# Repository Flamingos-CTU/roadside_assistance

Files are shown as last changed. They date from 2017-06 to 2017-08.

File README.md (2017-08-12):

# Roadside Assistance
Robot project repository for the Roadside Assistance competition on [Robot Day event](http://roboticday.org/2017/en/).

*Note: There is a hardware [notes](http://rtime.felk.cvut.cz/robot/index.php/M-BITBEAM_robot_kit) related to the robot and [m-bitbeam](http://www.tfsoft.cz/m-bitbeam/index_en.html) construction bit.*

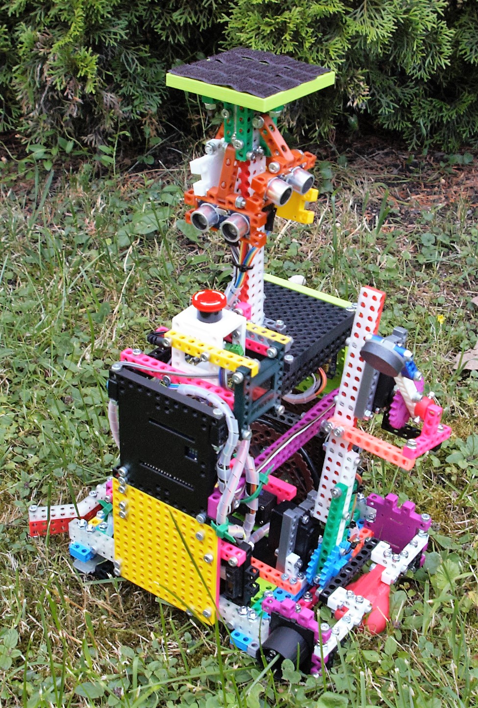
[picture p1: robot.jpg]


# Bit assistant

## Mission (impossible?)

The Roadside assistance contest is understood to be quite complicated and difficult.
Many robot creators think that a highly advanced control systems and algorithms, complicated electronics and mechanical design are needed to create a robot that can successfully attend this contest. Because of this there were not too many competitors to this contest to date.
We would like to change that and with our robot we want to present to the public that it can be done in a simple way.

Our goal is to build a robot from cheap and easily available components.
We want to build the robot as simple as possible yet potentially extensible to finish more tasks in the future.

## Robot

### Mechanical part

The robot construction is build exclusively from plastic 3D-printed parts connected with metal bolts and nuts.
These parts come from an open-hardware building kit called m-BITBEAM.
Source files for all the parts are freely available for download on GitHub (https://github.com/e-Mole/m-Bitbeam_Parts_for_3Dprint).
Any part can be easily reproduced/printed if needed.

The building kit is partially compatible with LEGO Technics/Mindstorms - the split of the mounting holes is the same.

The chassis uses a standard differential construction with two wheels and one support ball.

On the back of the robot is a robotic arm with three joints. Two of them are powered using servo motors. The end of the arm is fitted with a permanent magnet.
The arm is used to pick-up a spare battery and load it into the electric car.

### Hardware / electronics

#### Control logic

The control system of the robot is designed as a very simple distributed system comprising two Arduino boards.
The main control algorithm is programmed into Arduino UNO board with Servo shield attached.
This board drives all the servo motors and collect data from some sensors.

A second Arduino NANO board is used purely as a sensor gateway. It reads data from sensors and transmit the data to the main board.
The two Arduino boards are connected using simple serial line.

#### Sensoric sub-system

The robot is equipped with these sensors:
- 4x ultrasound module - used to detect the opponent.
- 2x infrared distance sensor on sides - used to detect playing elements (cars and batteries).
- 7x infrared reflective sensor at the bottom - used to detect color changes of the background of the playing field.
- 2x color sensor on sides - used to detect color of the electric cars.

#### Display, signalization, debuging

A small OLED graphic display is used to display various data.

Measured values from all the sensors and actual state of the control automaton are periodically transmitted on the USB-serial line.

#### Power supply

All the electronic components are supplied from a 5xAA NiMH battery pack.

### Software

The robot is based on the reactive paradigm. There is no environment map in the robot's memory. Just go ahead and follow the sensors' values.

Robot's behavior is implemented using finite state machines. We used feature-rich and powerful library Automaton. It also provides an extension for servo control. We implemented several separated automatons to control the robot:
* match automaton - starts the robot, check end of the match, handles sensor data received from sensor board,
* motion control automaton - drive servos and check the opponent to avoid a collision,
* automaton for a particular task, e.g. push_the_truck automaton handles such states as go_to_the_road, turn_on_the road, follow_the_road and push_the_truck.

Our software is available under the open source license. Go to Github and check it:) (https://github.com/Flamingos-CTU/roadside_assistance)

#### Tools

Software used in the robot was created using Arduino IDE. We also used a lot of freely available libraries and managed them by library manager built-in in Arduino IDE. We use Git for source code, hardware design and documentation versioning.

## About us

Our team is formed by three members - Matouš Pokorný, Michal Vokáč and Tomáš Novák.
We are a union of remnants of two independent teams - Flamingos and Gymspit.
We are also members of the organizational team of the Robotic Day.

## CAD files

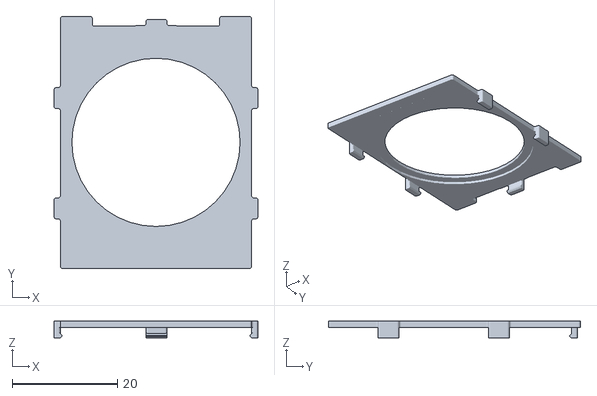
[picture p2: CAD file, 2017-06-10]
hw/colorSensor/lid.stl
38.8 x 48.0 x 3.20

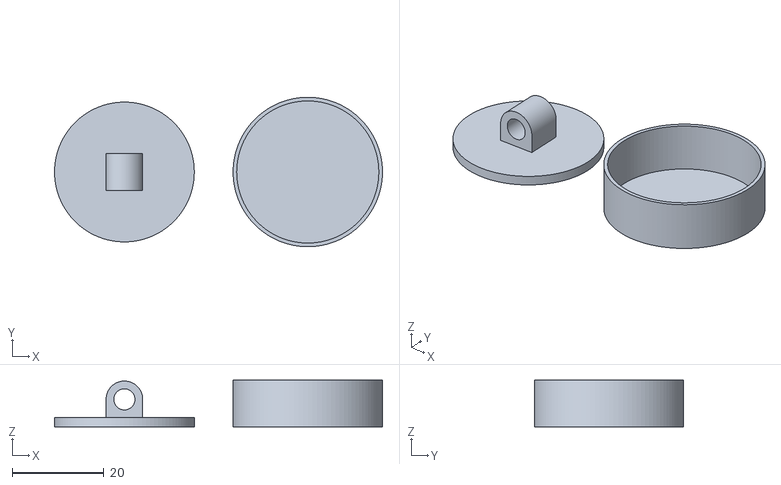
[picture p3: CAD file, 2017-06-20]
hw/magnet-holder/magnet-holder.stl
71.5 x 32.6 x 10.2

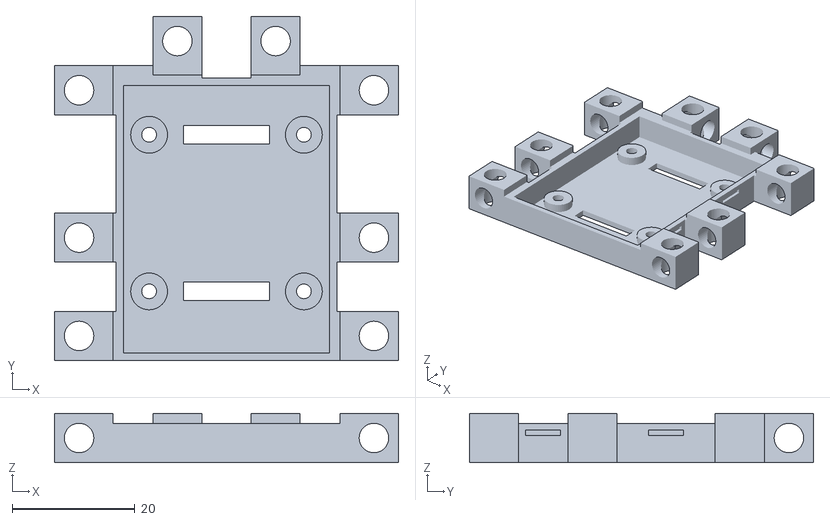
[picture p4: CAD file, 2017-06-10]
hw/colorSensor/box.stl
56.0 x 56.0 x 8.00

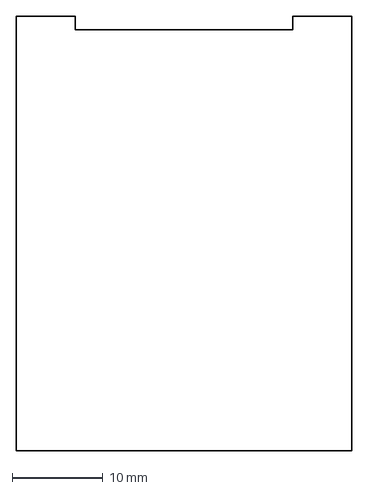
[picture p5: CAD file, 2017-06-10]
hw/colorSensor/molebox.dxf
37.0 x 48.0 mm

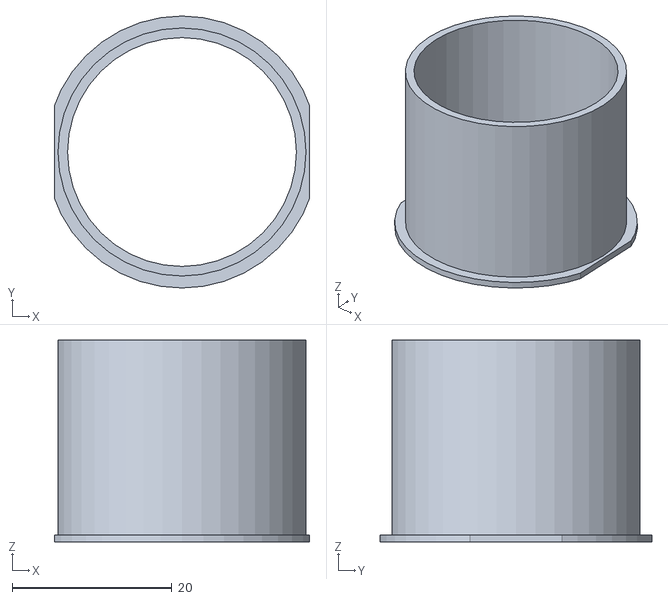
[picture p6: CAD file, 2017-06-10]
hw/colorSensor/cone.stl
31.9 x 34.0 x 25.2

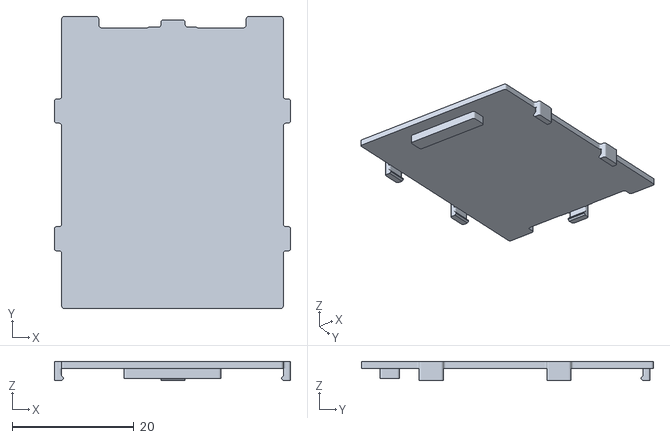
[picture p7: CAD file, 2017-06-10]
hw/colorSensor/bb-sen-uni-bt-c.stl
38.8 x 48.0 x 3.20

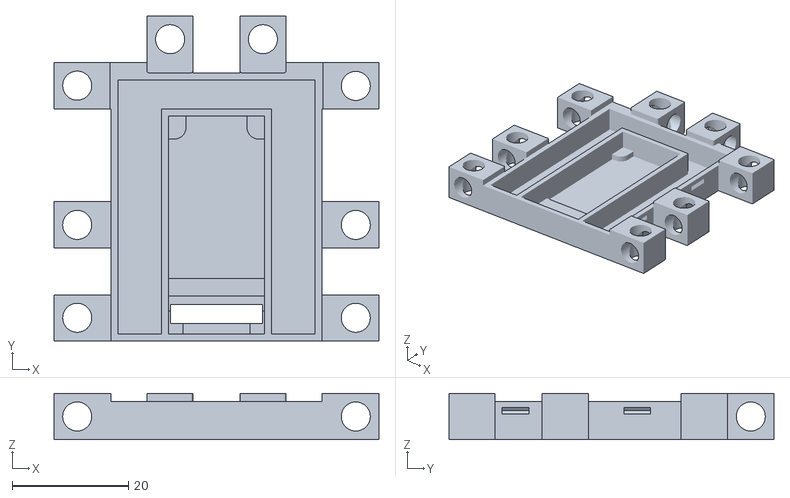
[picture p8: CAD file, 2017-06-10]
hw/colorSensor/bb-sen-uni-bt.stl
56.0 x 56.0 x 8.00

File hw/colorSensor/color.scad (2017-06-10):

$fn=40;
color([1,0,0]) colorbox();
color([0,0,1]) topcone();
lid();

module colorbox(){
    difference(){union(){
    basebox();
    translate([(28.4-3.2)/2,(28.7-3.2)/2,3/2])cylinder(d=6,h=3,center=true);
    translate([(28.4-3.2)/2,-(28.7-3.2)/2,3/2])cylinder(d=6,h=3,center=true);
    translate([-(28.4-3.2)/2,(28.7-3.2)/2,3/2])cylinder(d=6,h=3,center=true);
    translate([-(28.4-3.2)/2,-(28.7-3.2)/2,3/2])cylinder(d=6,h=3,center=true);
    }
    translate([(28.4-3.2)/2,(28.7-3.2)/2,2])cylinder(d=2.4,h=5,center=true);
    translate([(28.4-3.2)/2,-(28.7-3.2)/2,2])cylinder(d=2.4,h=5,center=true);
    translate([-(28.4-3.2)/2,(28.7-3.2)/2,2])cylinder(d=2.4,h=5,center=true);
    translate([-(28.4-3.2)/2,-(28.7-3.2)/2,2])cylinder(d=2.4,h=5,center=true);
    translate([0,-(28.7-3.2)/2,0])cube([14,3,4],center=true);
    translate([0,(28.7-3.2)/2,0])cube([14,3,4],center=true);
    }
}


module lid(){
difference(){translate([-100+8,-48/2,0])import("bb-sen-uni-bt-c.stl");
    cylinder(h=20,d=32);
    translate([0,-20,(8-1.2)/2-0.205])cube([25,10,8-1.2],center=true);
    cylinder(d=36,h=7.1);
    }
}
    
module topcone(){
    intersection(){
    translate([0,0,5])difference()
    {union(){
        translate([0,0,0.45])cylinder(d=34,h=0.9,center=true);
        translate([0,0,25.25/2])cylinder(d=31,h=24+1.25,center=true);
        }
        translate([0,0,25.25/2])cylinder(d=31-2.4,h=24+1.25+0.2,center=true);
        }
        linear_extrude(height=400)scale([0.95,0.95,1])translate([-56/2,-48/2,0])import("molebox.dxf",layer="innerbox");
    }
    }
module basebox(){
    translate([-56/2,-48/2,0])difference(){linear_extrude(height=8) import("molebox.dxf",layer="0",convexity=10);
translate([0,0,1.25])linear_extrude(height=8) import("molebox.dxf",layer="innerbox");
translate([0,0,6.35])linear_extrude(height=8) import("molebox.dxf",layer="lid",convexity=10);
    translate([4,4,4]) doublehole();
    translate([4,4+16,4]) doublehole();
    translate([4,4+40,4]) doublehole();
    translate([4+48,4,4]) doublehole();
    translate([4+48,4+16,4]) doublehole();
    translate([4+48,4+40,4]) doublehole();
    translate([4+16,4+48,4]) rotate([0,0,90])doublehole();
    translate([4+32,4+48,4]) rotate([0,0,90])doublehole();
        translate([10,4+8,6.35-1.5]) cube([1.2,5.7,0.9],center=true);
        translate([10,4+28,6.35-1.5]) cube([1.2,5.7,0.9],center=true);
        translate([46,4+8,6.35-1.5]) cube([1.2,5.7,0.9],center=true);
        translate([46,4+28,6.35-1.5]) cube([1.2,5.7,0.9],center=true);
        translate([56/2,56-10,6.35-1.5]) cube([5.7,1.2,0.9],center=true);
    }
}
module doublehole(){
    union(){
        cylinder(d=4.8,h=9,center=true);
        rotate([90,0,0])cylinder(d=4.8,h=9,center=true);
        }
        }

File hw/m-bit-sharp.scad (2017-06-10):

$fn=50;
translate([0,-4,0])union(){
difference(){
    translate([0,4,0]) cube([48,16,8],center=true);
    translate([0,3,2.5]) cube([45.5,15,8],center=true);
    translate([-37/2,3.5,0]) cylinder(h=10,d=2,center=true);
    translate([37/2,3.5,0]) cylinder(h=10,d=2,center=true);
    //translate([0,-8,1.5]) cube([11,10,8],center=true);    
}
translate([-28,8,0])rotate([0,0,90])beam(1,1,true);
translate([-28,-8,0])rotate([0,0,90])beam(1,1,true);
translate([28,-8,0])rotate([0,0,90])beam(1,1,true);
translate([-16,-8,0])rotate([0,0,90])beam(1,2);
translate([16,-8,0])rotate([0,0,90])beam(1,2);
translate([28,8,0])rotate([0,0,90])beam(1,1,true);
translate([8,16,0])rotate([0,0,0])beam(1,1,true);
translate([-8,16,0])rotate([0,0,0])beam(1,1,true);
translate([0,-8,-1.5])cube([16,8,5],center=true);
}



module beam(width,height, horizontal=false){
    difference(){
        union(){
            cube([8*(width),8*height,8], center=true);
        }
        for(i=[-(8*(height/2+0.5)):8:(8*(height/2+0.5))])
            for(j=[-8*(width/2-0.5):8:(8*(width/2-0.5))])
                translate([j,i,0])cylinder(d=5,h=9,center=true);
        if(horizontal){
            for(i=[-(8*(height/2+0.5)):8:(8*(height/2+0.5))])
                for(j=[-8*(width/2-0.5):8:(8*(width/2-0.5))])
                    translate([j,i,0]) rotate([0,90,0])cylinder(d=5,h=9,center=true);
        }
    }
}

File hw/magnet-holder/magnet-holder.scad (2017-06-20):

$fn=100;
cylinder(d=30.5, h=2);
translate([0,0,6])difference(){union(){translate([0,0,-2])cube([8,8,4],center=true);
    translate([0,0,0]) rotate([90,0,0]) cylinder(d=8,h=8,center=true);}
    rotate([90,0,0])cylinder(d=4.6, h=20,center=true);
    };
    
translate([40,0,0]){
    difference(){cylinder(d=31+1.6,h=10.2);
        translate([0,0,0.2])cylinder(d=31,h=20);
    }
    }

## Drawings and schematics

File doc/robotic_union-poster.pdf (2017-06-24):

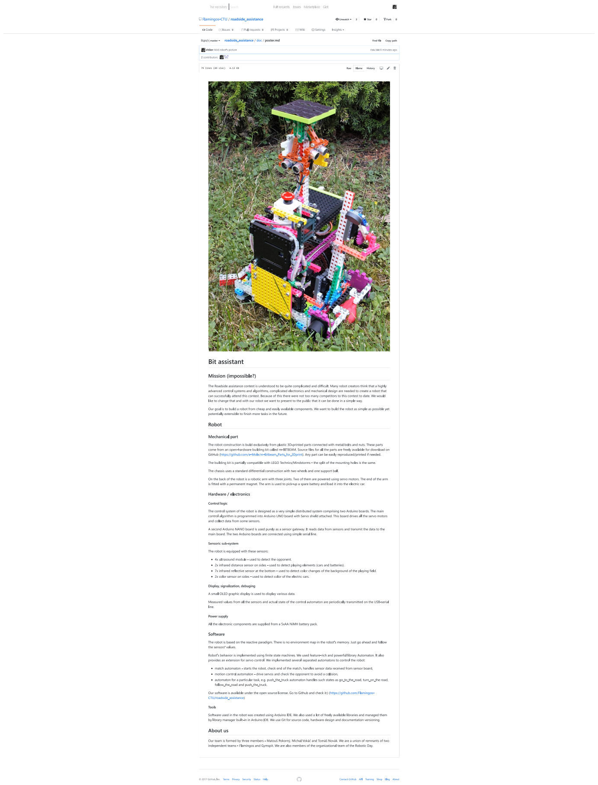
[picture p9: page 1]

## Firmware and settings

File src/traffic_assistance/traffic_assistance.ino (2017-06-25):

#include <Automaton.h>
#include "Atm_traffic_assistance.h"
#include "Atm_differential_motion.h"
#include "Pin_layout.h"

// Sketch for main Arduino board executing match finite state machine (FSM)

// Match FSM
Atm_traffic_assistance traffic_assistance;
// Start button FSM
Atm_button button;

char sensor_buffer[40];
Atm_command sensor_board;
//Atm_timer sensor_data_timer;
Atm_differential_motion motion;

//constexpr uint16_t sensor_data_timeout = 1000; // ms
constexpr uint16_t sharpThresh=200;

constexpr uint8_t obstacleThresh = 40; // obstackle detected if closer than this distance in cm
constexpr uint8_t blackThresh = 20; // black color when sensor output above this value 

struct sens_environment environment;

enum {
  ST,
  UF,       // Front ulstrasound sensor,
  UB,       // back (rear),
  UL,       // left,
  UR,       // right.
  LL,       // Left front line sensor,
  LR,       // front right,
  LML,      // middle left,
  LMR,      // middle right,
  LC,       // center.
  LRL,      // rear left
  LRR       // rear right
};

constexpr char sensor_list[] = "ST";

void on_sensor_data(int idx, int v, int up)
{
  static uint8_t loopCounter=0;
  switch(v) {
    case ST:
        //sensor_data_timer.start();
        environment.obstacleFront = atoi(sensor_board.arg(UF)) > 0 && atoi(sensor_board.arg(UF)) < obstacleThresh;
        environment.obstacleBack = atoi(sensor_board.arg(UB)) > 0 && atoi(sensor_board.arg(UB)) < obstacleThresh;
        environment.obstacleLeft = atoi(sensor_board.arg(UL)) > 0 && atoi(sensor_board.arg(UL)) < obstacleThresh;
        environment.obstacleRight = atoi(sensor_board.arg(UR)) > 0 && atoi(sensor_board.arg(UR)) < obstacleThresh;
        environment.blackLM = atoi(sensor_board.arg(LC)) > blackThresh;
        environment.blackLL = atoi(sensor_board.arg(LL)) > blackThresh;
        environment.blackLR = atoi(sensor_board.arg(LR)) > blackThresh;
        environment.blackLML = atoi(sensor_board.arg(LML)) > blackThresh;
        environment.blackLMR = atoi(sensor_board.arg(LMR)) > blackThresh;        
        environment.sharpLObst = analogRead(0) > sharpThresh;
        environment.sharpRObst = analogRead(1) > sharpThresh;
        uint8_t right = analogRead(3) >> 2;
        uint8_t left = analogRead(2) >> 2;
        environment.blackLRR = right > blackThresh;
        environment.blackLRL = left > blackThresh;
        if(((++loopCounter) & 0x1F) == 0 ){
            Serial.println();
            Serial.println("sensor_board:\tUF\tUB\tUL\tUR\tLL\tLR\tLML\tLMR\tLC\tLRL\tLRR\tS1\tS2");
            Serial.print("raw_values:");
            for(uint8_t i=1;i<=9;i++){
                Serial.print("\t");
                Serial.print(sensor_board.arg(i));
            }
            Serial.print("\t");
            Serial.print(left,DEC);
            Serial.print("\t");
            Serial.print(right,DEC);
            Serial.println();
            Serial.print("detection:\t");
            Serial.print(environment.obstacleFront?1:0,DEC);
            Serial.print("\t");
            Serial.print(environment.obstacleBack,DEC);
            Serial.print("\t");
            Serial.print(environment.obstacleLeft,DEC);
            Serial.print("\t");
            Serial.print(environment.obstacleRight,DEC);
            Serial.print("\t");
            Serial.print(environment.blackLL,DEC);
            Serial.print("\t");
            Serial.print(environment.blackLR,DEC);
            Serial.print("\t");
            Serial.print(environment.blackLML,DEC);
            Serial.print("\t");
            Serial.print(environment.blackLMR,DEC);
            Serial.print("\t");
            Serial.print(environment.blackLM,DEC);
            Serial.print("\t");
            Serial.print(environment.blackLRL,DEC);
            Serial.print("\t");
            Serial.print(environment.blackLRR,DEC);
            Serial.print("\t");
            Serial.print(analogRead(0),DEC);
            Serial.print("\t");
            Serial.print(analogRead(1),DEC);
            Serial.println();
        }
  }
}

void setup() {
  // Init main serial line for programming and debugging purposes
  Serial.begin(115200);
  traffic_assistance.trace(Serial);
  button.trace(Serial);
 
  // Init FSMs
  traffic_assistance.begin();
  //sensor_data_timer.begin(sensor_data_timeout);
  //sensor_data_timer.start();
  
  button.begin(start_button_pin).onPress([] (int idx, int v, int up) {
    traffic_assistance.trigger(traffic_assistance.EVT_START);
  });
  pinMode(8, OUTPUT);           // set pin to input
  digitalWrite(8, LOW); 
  sensor_board.begin(Serial, sensor_buffer, sizeof(sensor_buffer))
    .list(sensor_list)
    .onCommand(on_sensor_data,1);
  //sensor_data_timer.trace(Serial);
  motion.begin();
  motion.trace(Serial);
}

void loop() {
  automaton.run();
}

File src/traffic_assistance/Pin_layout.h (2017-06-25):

#pragma once

constexpr int start_button_pin = 2;
constexpr int servo_left = 5;
constexpr int servo_right = 6;

constexpr uint8_t leftServoZeroPos = 88;
constexpr uint8_t rightServoZeroPos = 87;

struct sens_environment{
  bool obstacleFront;
  bool obstacleLeft;
  bool obstacleBack;
  bool obstacleRight;
  bool blackLM; // line sensor middle detecting black
  bool blackLL; // line sensor front left detecting black
  bool blackLR; // line sensor front right detecting black
  bool blackLML;// line sensor front middle left detecting black
  bool blackLMR;// line sensor front middle right detecting black
  bool blackLRL;// line sensor rear middle left detecting black
  bool blackLRR;// line sensor rear middle right detecting black
  bool sharpLObst;
  bool sharpRObst;
  };

  constexpr int default_speed=10;

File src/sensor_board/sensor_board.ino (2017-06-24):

#include <Ultrasonic.h>

constexpr long scan_period = 100; //period of measurement of data


Ultrasonic ul(6, 7, 10000UL);  // left ultrasonic sensor HC-04
Ultrasonic ur(8, 9, 10000UL);  // right ultrasonic sensor HC-04
Ultrasonic ub(10, 11, 10000UL);  // back ultrasonic sensor HC-04
Ultrasonic uf(12, 13, 10000UL);  // front ultrasonic sensor HC-04

enum {
  UF,       // Front ulstrasound sensor,
  UB,       // back (rear),
  UL,       // left,
  UR,       // right.
  LL,       // Left front line sensor,
  LR,       // front right,
  LML,      // middle left,
  LMR,      // middle right,
  LC,       // center.
  NOS       // Number of sensors
};

uint8_t sens_vals[NOS];

void setup() {
  // hardware serial used for debugging
  Serial.begin(115200);
  // software serial used for communication with main board
  Serial1.begin(115200);
  pinMode(5, INPUT);           // set pin to input
  digitalWrite(5, HIGH); 
}

void loop() {
  long scan_start = millis();

  // reading ultrasonic distances
  sens_vals[UF] = uf.distanceRead(CM);
  sens_vals[UB] = ub.distanceRead(CM);
  sens_vals[UL] = ul.distanceRead(CM);
  sens_vals[UR] = ur.distanceRead(CM);

  // reading line sensors values
  // value is converted to range 0..255 (originaly was 0..1024)
  sens_vals[LL] = analogRead(1)>>2; 
  sens_vals[LR] = analogRead(3)>>2;
  sens_vals[LML] = analogRead(0)>>2;
  sens_vals[LMR] = analogRead(4)>>2;
  sens_vals[LC] = analogRead(2)>>2;
  
  long send_start = millis();
  if(digitalRead(5)==0){
      Serial1.begin(115200);
      // send the data
      Serial1.print("ST");
      for(int i=0; i<NOS; i++){
        Serial1.print(" ");
        Serial1.print(sens_vals[i], DEC);
      }
      Serial1.println();
  }
  else{
      Serial1.end();  
  }
  
  //debugging output... length of measurement
  Serial.print("measure time: ");
  Serial.println(send_start-scan_start,DEC);

  //debugging output... length of measurement
  Serial.print("sending time: ");
  Serial.println(millis()-send_start,DEC);

  // wait for next period start
  while(millis()< (scan_start + scan_period));
}

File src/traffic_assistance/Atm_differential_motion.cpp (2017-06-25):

#include "Atm_differential_motion.h"
#include "Pin_layout.h"
/* Add optional parameters for the state machine to begin()
 * Add extra initialization code
 */

extern sens_environment environment;

Atm_differential_motion& Atm_differential_motion::begin( void ) {
  // clang-format off
  const static state_t state_table[] PROGMEM = {
    /*             ON_ENTER  ON_LOOP    ON_EXIT  EVT_COMMAND_CHANGED  EVT_NO_OPPONENT  EVT_OPPONENT_DETECTED  EVT_GO_IDLE  EVT_TIMEOUT  ELSE */
    /*   IDLE */   ENT_IDLE,      -1,  EXT_IDLE,              MOVING,              -1,                    -1,          -1,          -1,   -1,
    /* MOVING */ ENT_MOVING,      -1,        -1,              MOVING,              -1,                 PAUSE,        IDLE,        IDLE,   -1,
    /*  PAUSE */  ENT_PAUSE,      -1, EXT_PAUSE,              MOVING,          MOVING,                    -1,        IDLE,        IDLE,   -1,
  };
  // clang-format on
  Machine::begin( state_table, ELSE );
  left.begin(servo_left,leftServoZeroPos).step(1,30).trace(Serial);
  right.begin(servo_right, rightServoZeroPos).step(1,30).trace(Serial);
  return *this;          
}

/* Add C++ code for each internally handled event (input) 
 * The code must return 1 to trigger the event
 */

int Atm_differential_motion::event( int id ) {
  switch ( id ) {
    case EVT_COMMAND_CHANGED:
      return 0;
    case EVT_NO_OPPONENT:
      return 1-event(EVT_OPPONENT_DETECTED);
    case EVT_OPPONENT_DETECTED:
      if(lspeed > 0 && rspeed < 0 && (environment.obstacleFront || environment.sharpLObst || environment.sharpRObst))
          return 1;
      if(lspeed < 0 && rspeed > 0 && environment.obstacleBack)
          return 1;
      if((environment.obstacleLeft || environment.obstacleRight || environment.obstacleFront || environment.sharpLObst || environment.sharpRObst) && ((lspeed >0 && rspeed>0)||(lspeed<0&&rspeed<0)))
          return 1;
      return 0;
    case EVT_GO_IDLE:
      return 0;
    case EVT_TIMEOUT:
      return 0;
  }
  return 0;
}

/* Add C++ code for each action
 * This generates the 'output' for the state machine
 */

void Atm_differential_motion::action( int id ) {
  switch ( id ) {
    case ENT_IDLE:
      return;
    case EXT_IDLE:
      return;
    case ENT_MOVING:
      return;
    case ENT_PAUSE:
      left.step(180,0).position(leftServoZeroPos);
      right.step(180,0).position(rightServoZeroPos);
      return;
    case EXT_PAUSE:
      left.step(1,30).position(leftServoZeroPos + lspeed);
      right.step(1,30).position(rightServoZeroPos + rspeed);
      return;
  }
}

/* Optionally override the default trigger() method
 * Control how your machine processes triggers
 */

Atm_differential_motion& Atm_differential_motion::trigger( int event ) {
  Machine::trigger( event );
  return *this;
}

/* Optionally override the default state() method
 * Control what the machine returns when another process requests its state
 */

int Atm_differential_motion::state( void ) {
  return Machine::state();
}

Atm_differential_motion& Atm_differential_motion::forward(int speed){
  lspeed = speed;
  rspeed = -speed;
  left.step(1,30).position(leftServoZeroPos + speed);
  right.step(1,30).position(rightServoZeroPos - speed);
  trigger(EVT_COMMAND_CHANGED);
  return *this;
}

Atm_differential_motion& Atm_differential_motion::turn(int speed){
  lspeed = speed;
  rspeed = speed;
  
  left.step(1,30).position(leftServoZeroPos + speed);
  right.step(1,30).position(rightServoZeroPos + speed);
  trigger(EVT_COMMAND_CHANGED);
  return *this;
}

Atm_differential_motion& Atm_differential_motion::stop(){
  lspeed = 0;
  rspeed = 0;
  left.step(180,0).position(leftServoZeroPos);
  right.step(180,0).position(rightServoZeroPos);
  trigger(EVT_GO_IDLE);
  return *this;
}

/* Nothing customizable below this line                          
 ************************************************************************************************
*/

/* Public event methods
 *
 */

Atm_differential_motion& Atm_differential_motion::command_changed() {
  trigger( EVT_COMMAND_CHANGED );
  return *this;
}

Atm_differential_motion& Atm_differential_motion::no_opponent() {
  trigger( EVT_NO_OPPONENT );
  return *this;
}

Atm_differential_motion& Atm_differential_motion::opponent_detected() {
  trigger( EVT_OPPONENT_DETECTED );
  return *this;
}

Atm_differential_motion& Atm_differential_motion::go_idle() {
  trigger( EVT_GO_IDLE );
  return *this;
}

Atm_differential_motion& Atm_differential_motion::timeout() {
  trigger( EVT_TIMEOUT );
  return *this;
}

/* State trace method
 * Sets the symbol table and the default logging method for serial monitoring
 */

Atm_differential_motion& Atm_differential_motion::trace( Stream & stream ) {
  Machine::setTrace( &stream, atm_serial_debug::trace,
    "DIFFERENTIAL_MOTION\0EVT_COMMAND_CHANGED\0EVT_NO_OPPONENT\0EVT_OPPONENT_DETECTED\0EVT_GO_IDLE\0EVT_TIMEOUT\0ELSE\0IDLE\0MOVING\0PAUSE" );
  return *this;
}

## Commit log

2017-05-18 Added trace debug via serial line
2017-05-18 added pin layout for harware pins definitions
2017-05-18 added start function to traffic assistance automaton, added timer to count end of match
2017-06-10 color sensor molebox added
    [bb-sen-uni-bt-c.stl, bb-sen-uni-bt.stl, box.stl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]
2017-06-10 added sharp holder
    [m-bit-sharp.scad]
2017-06-10 update of color box
    [box.stl, color.scad, cone.stl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]
2017-06-10 updated colorbox
    [box.stl, color.scad, lid.stl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]
2017-06-20 magnet holder 3d model added
    [magnet-holder.scad, magnet-holder.stl]
2017-06-23 Add library to work with ultrasonic sensor
2017-06-23 Add library for Sharp infrared sensor
2017-06-23 Add library for TCS230 color sensor
2017-06-23 Add sketch to measure distance using Sharp IR sensor and display it on OLED
2017-06-23 Add sketch to display color from color sensor on a RGB LED and OLED display
2017-06-23 Change start button pin according to actual state
2017-06-23 Add sketch for sensor board
2017-06-23 Testing communication with sensor board
2017-06-23 finalized sensor board software, testing software with main board
2017-06-23 added fixed period sending, refactoring, comments updated
    [sensor_board.ino]
2017-06-23 added timeout to ultrasonic measurment with sensor_board, approximate 1.6m distance max measurement
2017-06-23 added debugging output -- sending time of uart communication
2017-06-23 added sensor processing
2017-06-24 switched from software serial due to clash with servo lib, added forward motion with differential drive
2017-06-25 finished automaton, not working
    [Atm_differential_motion.cpp, traffic_assistance.ino]
